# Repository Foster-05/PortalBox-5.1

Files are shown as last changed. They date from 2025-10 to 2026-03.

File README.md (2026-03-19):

# Portal Box 5.1.1
## A project by Bucknellians for Bucknellians, since 2013
   

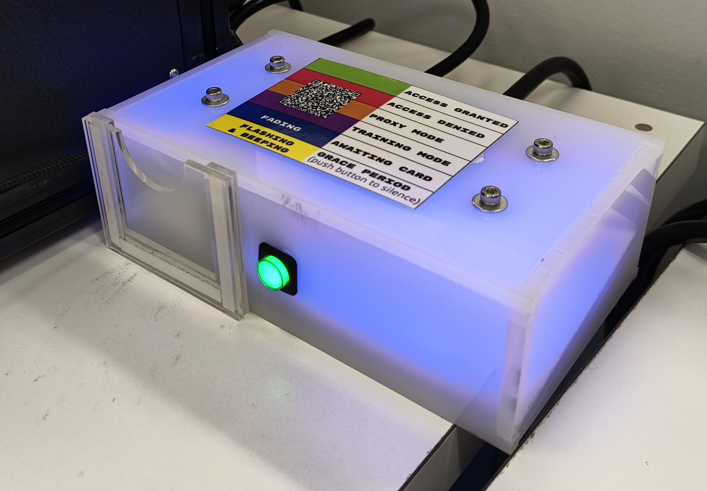
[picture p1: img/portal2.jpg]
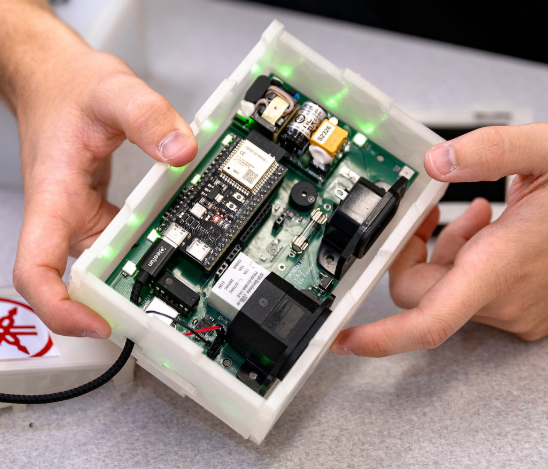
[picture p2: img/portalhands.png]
v5.0.6 while in progress
 

*The currently implemented Portalbox, v2, in the Maker-E connected to a Prusa XL (left) and a v5.0.6 prototype (right).*

## Background
The Portalbox is an open-source makerspace management project. It originated at Bucknell University, in our makerspace the "Maker-E", and intends to spread worldwide, allowing makerspaces to control their equipment and their users as they see fit. The Portalbox focuses on using interlocks to control power to equipment, such as 3D printers or laser cutters, based on the RFID cards that each student possesses. I had the opportunity to work on v5 of the Portalbox over the summer of 2025, continuing into the academic year 25-26.

The Portalbox has been an ongoing project for roughly a decade, remaining open-source and created by students throughout its lifetime. Professor Joe Hass and software engineer TKEgan on GitHub have historically maintained the project for both firmware and backend development, including but not limited to the database and website access that's used by student techs to change permissions to each Portalbox. Find more information about the backend at [their Github](https://github.com/Bucknell-ECE/PortalBox-ManagementPortal).

<details>

<summary> Previous Implementation </summary>

## Current Implementation

Current Portalbox implementation in the Maker-E

As it stands, the Portalbox is in the MakerE and for the most part, working as intended. It includes a very simple I/O: A slot for an RFID card, a simple pushbutton, and on the back two power ports and a reset button. It utilizes a finite state machine design to work with RFID reader and button input to ascern what mode of functionality it should be in. As much of this functionality has been retained for the next iteration. 

Use of the current Portalbox is very simple, intentionally so. Simply place your RFID card, programmed by a technician or makerspace administrator, into the card slot. The Portalbox will light blue if you are marked as certified in an SQL database, and red if you're not. If it determines that you are certified, it will activate the power interlock and allow wall power to flow to the machine that it's connected to, be it a 3D printer, laser cutter, or soldering iron. When you remove your card, the box will begin blinking yellow and beeping at you. Pressing the button on the front will exit this "grace mode". Putting your card back in will accomplish the same as putting your card in originally. However, if you place in a card programmed as a "proxy card", the box will light orange and remain on. The result is that you may use the machine or leave it running, but keep your assigned RFID card with you. Finally, if a user assigned as a trainer in the database takes their card out of the box, a non-certified user may place theirs as a replacement. The box will light purple for "training" mode, allowing the user to temporarily keep the equipment active while learning how to use it. After they have been trained on the piece of equipment a technician can certify them so they may use it in the future.

Moving into developing a Version 5, we maintained several goals in mind: shrinking the footprint, increasing speed and reliability, and maintaining or improving functionality. The physical box is significantly smaller than its predecessor, reducing by an overall 11 square centimeters. Our improved platform has yet to be tested firmware-wise, but we hope the new microcontroller will significantly improve response times and state detection accuracy. Our modular approach to design and implementation has allowed for increased functionality and the previous design with a slot and button is still available if users so wish.
</details>

<details open>
<summary>Technical information</summary>

## Technical
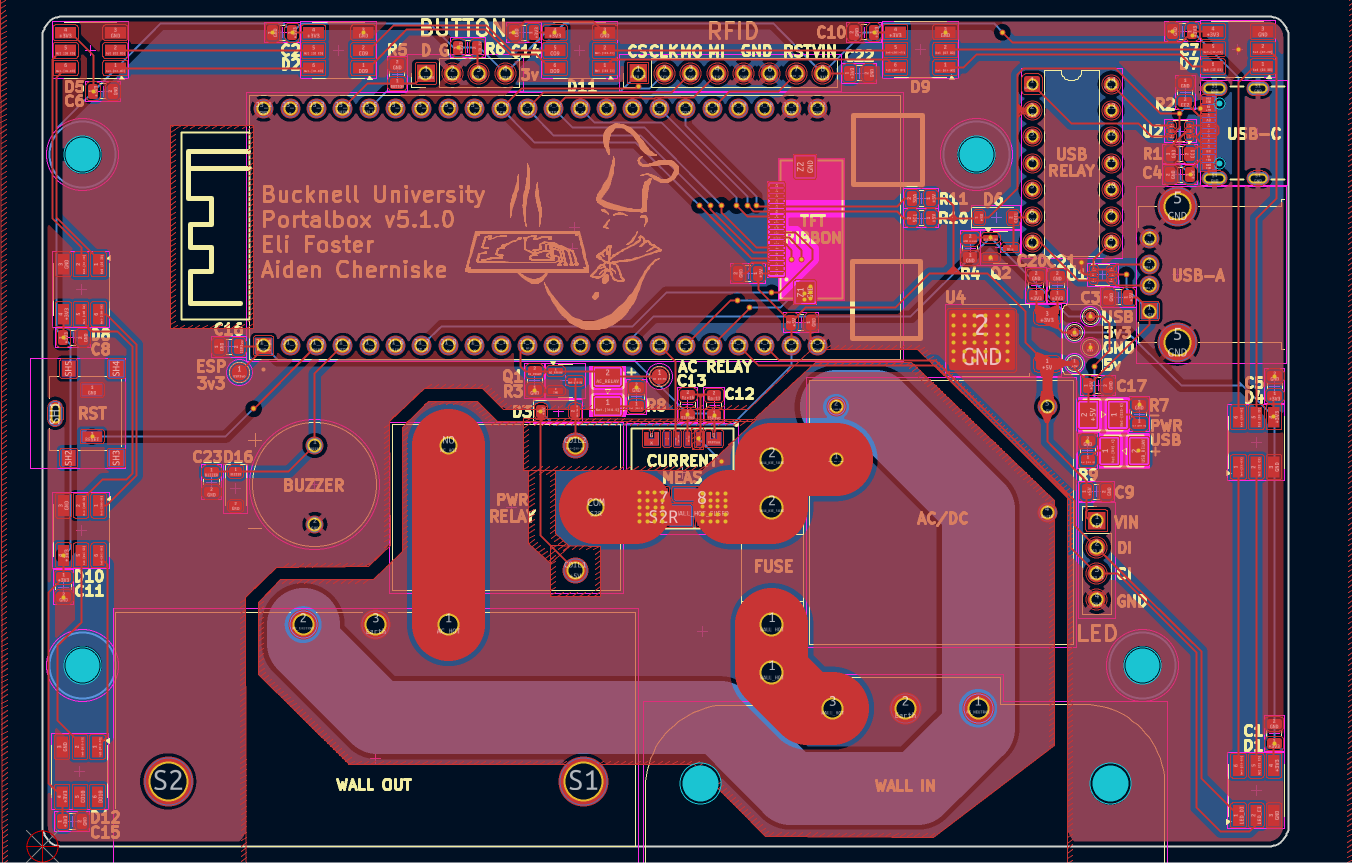
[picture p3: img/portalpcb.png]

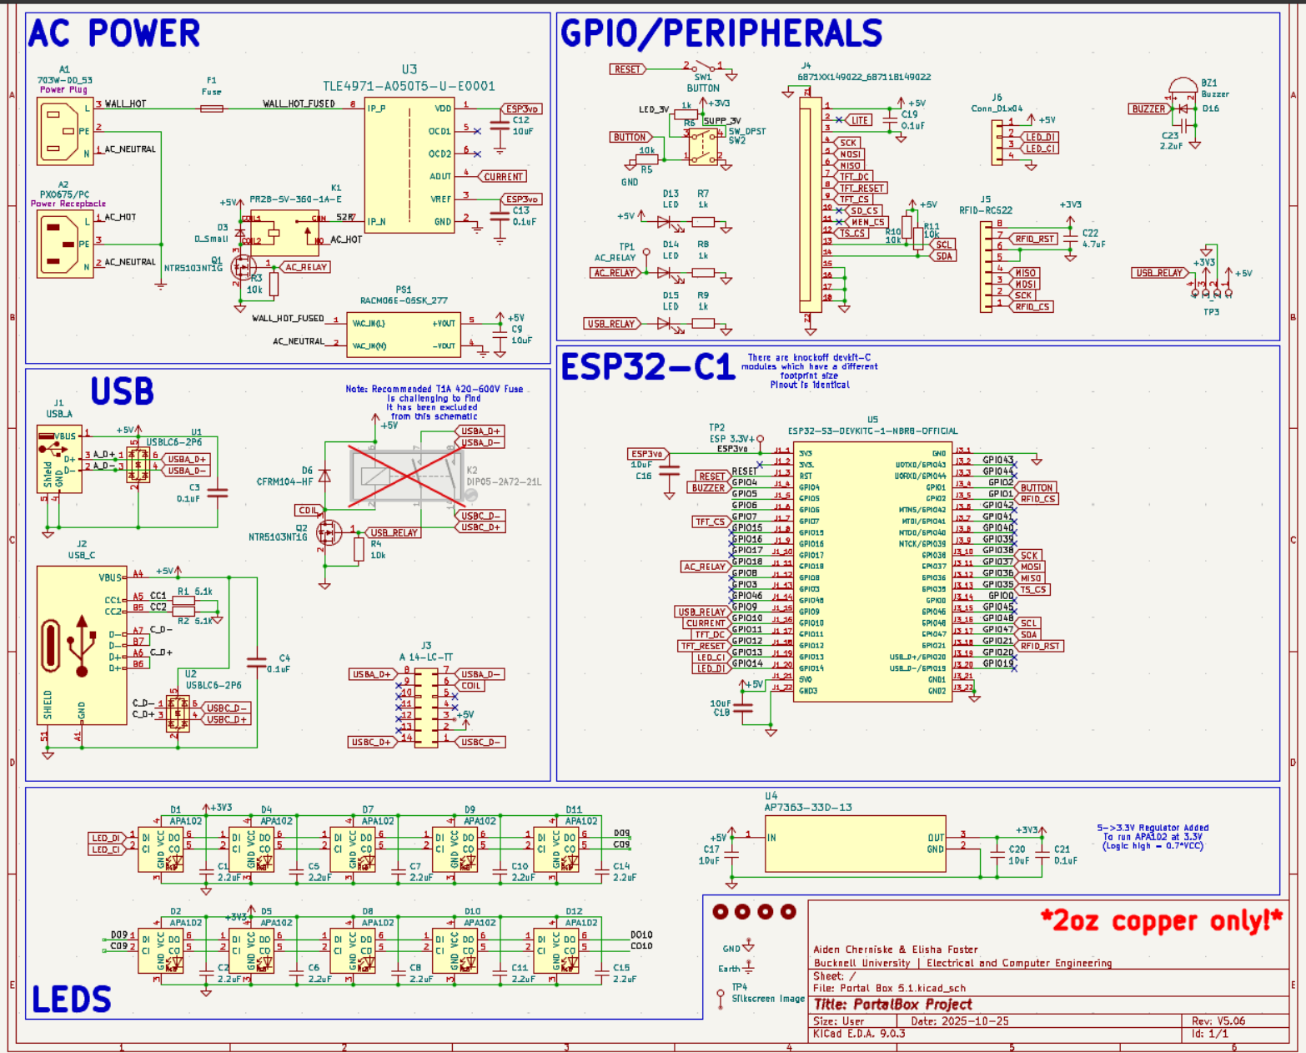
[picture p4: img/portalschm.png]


*Portalbox v5.1.0 layout (left) and schematic (right)*

<details>
<summary>Power Interlock</summary>

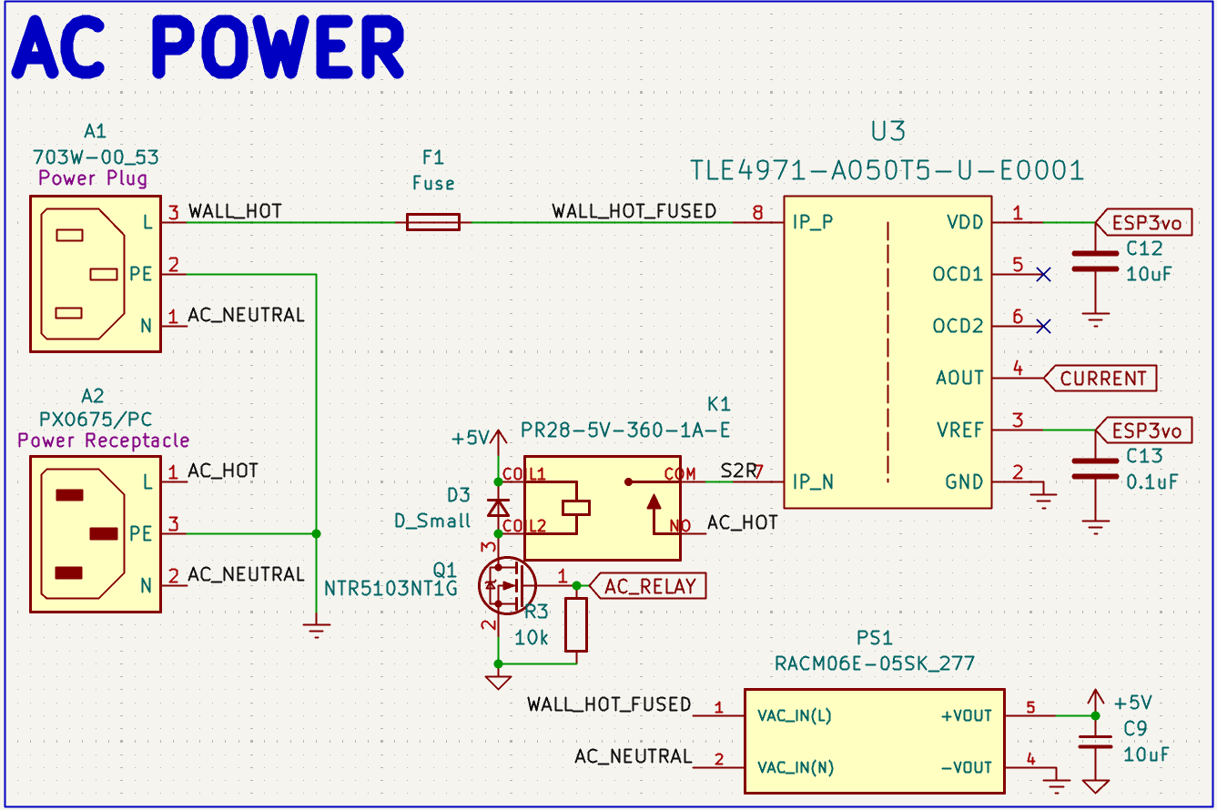
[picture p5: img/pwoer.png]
Schematic view of AC Power section for v5.1.0

### Overview
The Portalbox itself is powered off of 120Vrms from the wall, allowing for simpler placement and no worries or frustrations regarding battery power, lifetime, and so on. We use a hefty AC/DC converted to provide 5v power to the rest of the Portalbox, including the ESP32. We use relays to interlock wall power in between our two ports, one IEC C13 and one IEC C14. The female C13 is intended to be connected to wall power, while the male C14 is 15A fused output to makerspace equipment. We also include a current measurement IC to monitor power draw from a machine and monitor relay accuracy. Ensure that only 2 ounce copper is used when manufacturing: trace widths have been calculated to 2oz and traces may turn into fuses if incorrectly manufactured.
### Relay
We chose a [CUI Devices 20A relay](https://www.digikey.com/en/products/detail/same-sky-formerly-cui-devices/PR28-5V-360-1A-E/22522201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 "Digikey") to ensure that our fuse would disconnect the circuit before any parts become damaged. The relay accepts the hot line from the wall and outputs it to the current measurement IC when the relay is activated. Activation is done using a simple [NMOS transistor](https://www.digikey.com/en/products/detail/diodes-incorporated/2N7002K-7/1934378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 "Digikey") circuit to allow for a 3v GPIO pin from the ESP32 to activate the relay using 5v (its required activation voltage). This specific transistor was chosen for availability, being pre-stocked in our space.

### Current Measurement
We're measuring current flowing from the wall out to the C14 port for a multitude of reasons. With proper implementation, this would allow for a measurement of "normal" current draw for any given machine, thus allowing continuous monitoring and flagging of any unusual or concerning behavior remotely. It would also allow us to retrieve records or throw a flag if our maximum of 15A is reached, thus requiring us to replace the onboard fuse. This would require some implementation with the existing MariaDB SQL database to store said current data and/or flags. Measurement is accomplished using an [Infineon IC](https://www.digikey.com/en/products/detail/infineon-technologies/TLE4971A050T5UE0001XUMA1/18700354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 "Digikey") for this specific purpose. It's capable of +-120A, being much more than we need. It ouputs a variable voltage that depends on the current flowing through two major pads, allowing for later conversion into what specific current is being measured.
</details>

<details>
<summary>USB Interlock</summary>

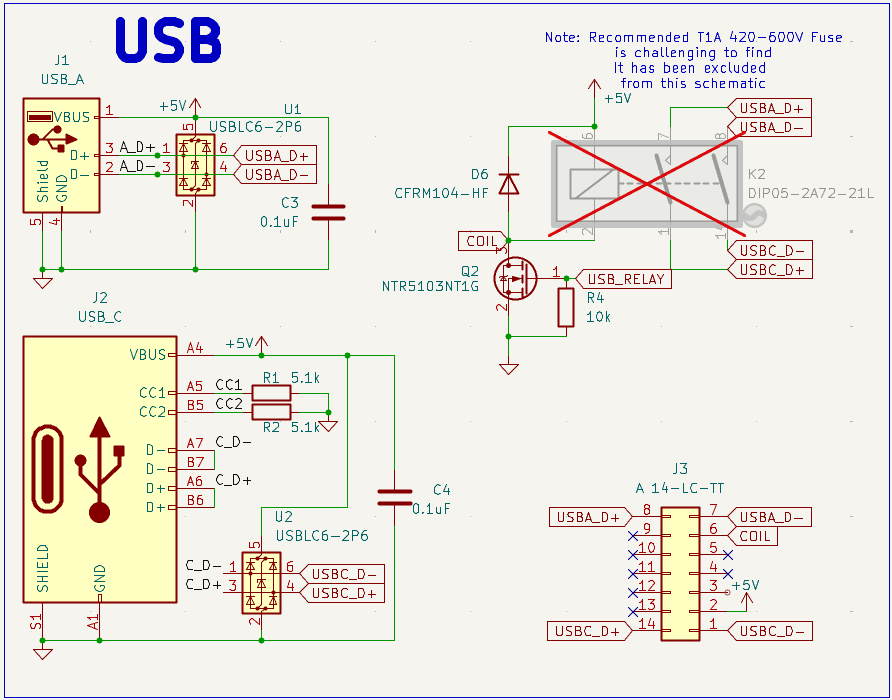
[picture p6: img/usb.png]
Schematic view of USB interlock section for v5.1.0

### Overview
The Portalbox is equipped to provide data interlock through USB 2.0 between a USB-A port and a USB-C port. This is for specific applications such as the Maker-E's laser cutter, where proprietary power supply makes power interlock difficult. However, one is able to connect USB cables in between the cutter and a dedicated device to restrict data transfer of files required for laser cutting. It uses a similar relay structure to the power interlock to allow for robust switching.

### Relay
We use a [Standex-Meder](https://www.digikey.com/en/products/detail/standex-meder-electronics/DIP05-2A72-21L/2765346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 "Digikey") DIP relay to allow for switching of data lines. It allows for simultaneous switching of two signals, which was necessary to interlock the D+/D- lines found in the USB 2.0 protocol. This particular relay may be out of stock and a Littelfuse equivealent is available. It's shown as excluded from the board in the schematic because we use a different [DIP header](https://www.digikey.com/en/products/detail/assmann-wsw-components/A-14-LC-TT/821743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 "Digikey") J3 to allow for active switching of relays. Modularity is a big focus of the Portalbox, so switching of any components is ideal when possible.

### USB port design
We use typical four-pin USB-A 2.0 ports as well as USB-C ports capable of 3.0 on the board files seen above. They follow best practices found in the datasheet for design, including but not limited to ESD protection with diode system ICs U1 and U2. Both ports are always powered with 5v and have no data connection unless the above relays are active.
</details>

<details>
<summary>Peripherals and GPIO</summary>

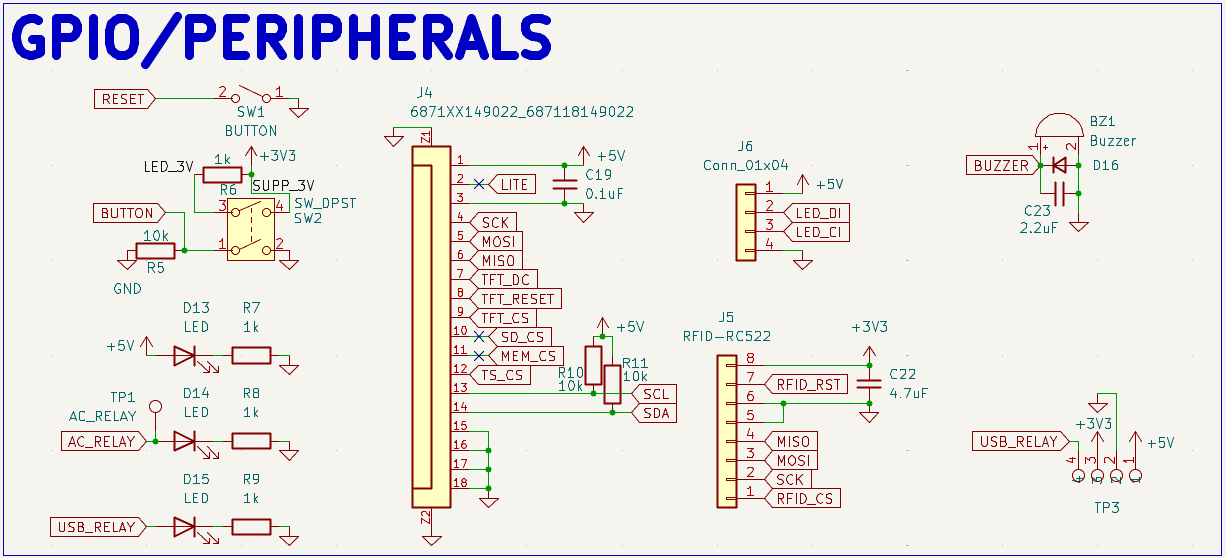
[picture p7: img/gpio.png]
Schematic view of GPIO section for v5.1.0


While the power and data interlocks are the meat and potatoes of the Portalbox, our peripherals and GPIO is the seasoning. These focus on all of our miscellaneous functions, both new and old. Historically the boxes have been as simple to use as possible, including simply a card slot, single pushbutton, and RGB LEDs for feedback. This functionality has been retained, but we hope to significantly improve it for future use.

### Casing
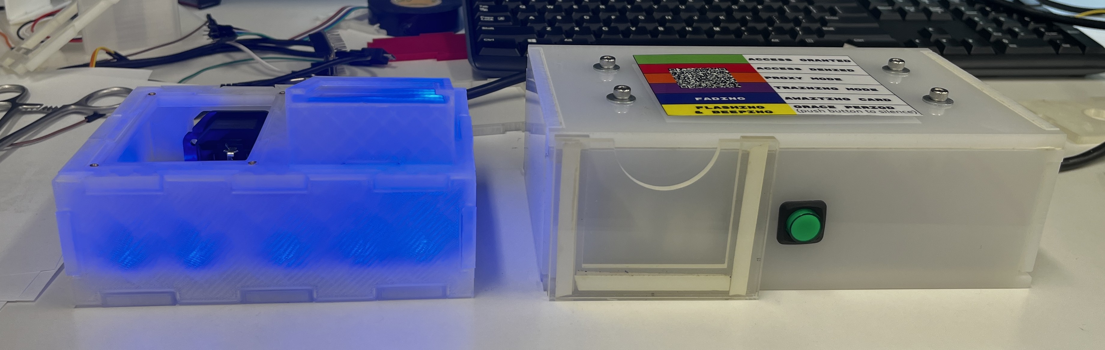
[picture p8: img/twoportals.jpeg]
Side-by-side old and new versions of the Portalbox.

Size has been another important factor of consideration while moving through the current version of the Portalbox. Initial versions were vertically stacked components, so they were relatively compact and fit in the space well. The versions currently implemented moved away from the vertical architecture, so they expanded significantly in footprint next to machinery in the Maker-E. Beginning our project, we wanted to ensure that we could shrink this footprint at least a little bit so the Portalbox would be more usable and widely applicable for most makerspaces. Above is pictured a version 5.0.6 (left), which is the same size as a version 5.1, next to a currently implemented Portalbox (right). The difference is apparent.

#### Materials and Design

Previously Portalboxes were all made out of lasercut acrylic, which was intentionally a semi-transparent material designed to be opaque but let LED light through to color the box itself. This design has worked very well, but we had serveral quarrels with it when starting the project. First and foremost, it was very painful to construct. The pieces had to fit together very precisely and use Very Heavy Bond tape to stick together long-term. The acrylic material was also expensive to acquire. We found that the original reasoning to choose acrylic was that makerspaces would be able to manufacture their own cases if they had a laser cutter on hand, as we did. Considering this design decision, we chose to move the Portalbox to a 3D printed enclosure. Nowadays, especially in the ECE space, 3D printers are a staple of iterative design and most makerspaces have access to at least one. We tested multiple filament types and determined that Jessie Transparent PLA was strong yet still let through the appropriate amount of light from LEDs mounted on the board. Gyroid infill patterns also provide fun effects! While designing the case, we were focused on ensuring modularity and ease of use. The case is designed to snap together using dovetails and require no adhesive or tape to stay together long-term. Said dovetails also provide interesting opportunities for modularity.

#### Modularity

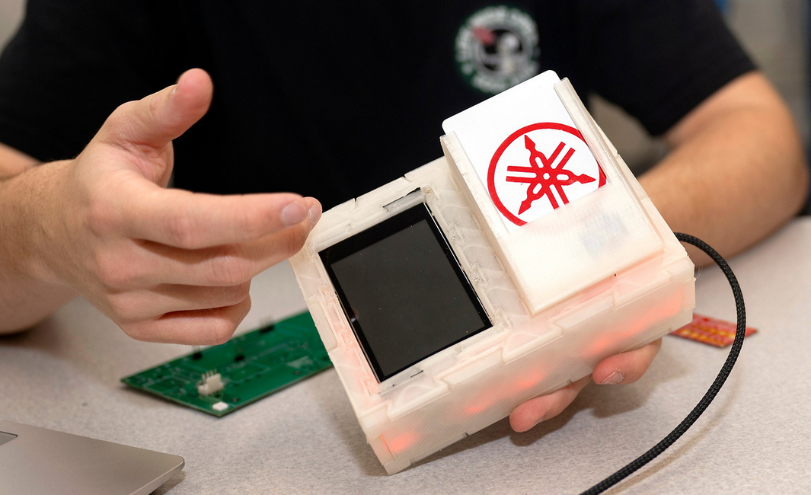
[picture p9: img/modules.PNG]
Top side of the Portalbox showcasing a card reader and touchscreen module installed.

Utilizing the 3D printed nature of the case and the dovetail design, we determined a method to standardize our design and allow for some of the open-source mindset to enhance the Portalbox. First and foremost, the Portalbox case was designed with options in mind. There are multiple inputs and outputs that one can choose to use with the Portalbox and that will work natively and immediately with the firmware, all of which have case pieces designed to fit them. There are also options to fit the same inputs and outputs on different sides of the case for alternate mounting options. The peak of modularity can be seen on the top part of the case, where it simply features two large holes containing dovetails to slot other pieces into. With this design, we're able to manufacture modules which best fit our use-case: from touchscreens to buttons to card readers, it provides nearly unlimited opportunity to design what you want for your makerspace and customize your Portalbox appropriately. We hope that the nature of this design will encourage others to participate and begin designing alternate components that will work with all the previous ones we've provided as a starting point.

### User Feedback

Along with the above mention of modularity, we wanted to ensure that this version of the Portalbox would be able to continue in its current function as well as extend to new applications. Therefore, we kept all of the same standard inputs and outputs: a piezo buzzer to alert users, RGB addressable LEDs to provide status of the box, a simple button for a multifunctional input, and an RFID reader for the typical "slot" application. We also extended some of the more technical user feedback by including test points for important nets, as well as mono-color feedback LEDs for 5v power, AC relay activation, and USB relay activation. A reset button broken out to the user is also available in the case of a manual reset becoming necessary. However, with the aforementioned modular case, we also included some other options for administrators. The firmware provides for a "tap" mode, where users no longer have to leave their card inside a Portalbox to use equipment. They can simply tap it on the case, and a "proxy" mode will be handled all in software instead of requiring physical proxy cards. We also added a ribbon cable connector for Adafruit's Eye-SPI technology, making interfacing with one of their [ILI9341 capacitative touch displays](https://www.adafruit.com/product/2090 "Adafruit") simple to implement. We hope that this will spruce up our space and make the Portalboxes even easier to use, while not precluding previous use-cases.
</details>

<details>
<summary>Microcontroller</summary>

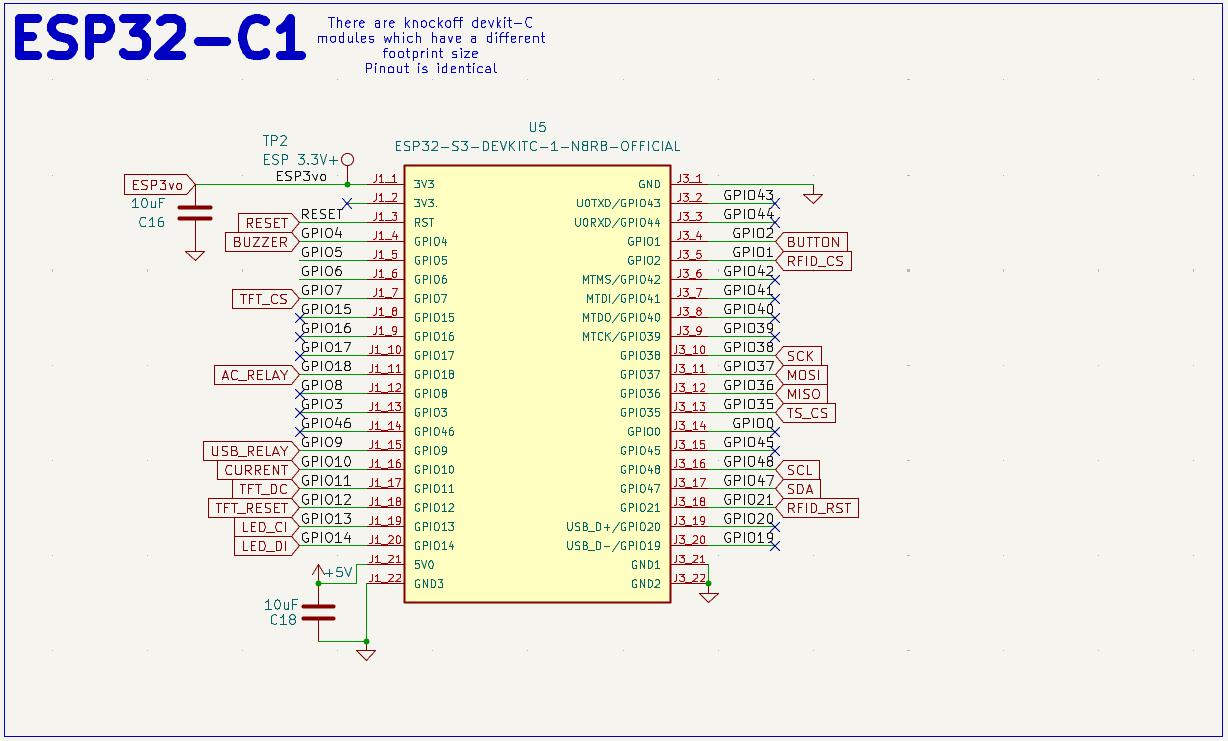
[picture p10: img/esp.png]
Schematic view of MCU section for v5.1.0

### History
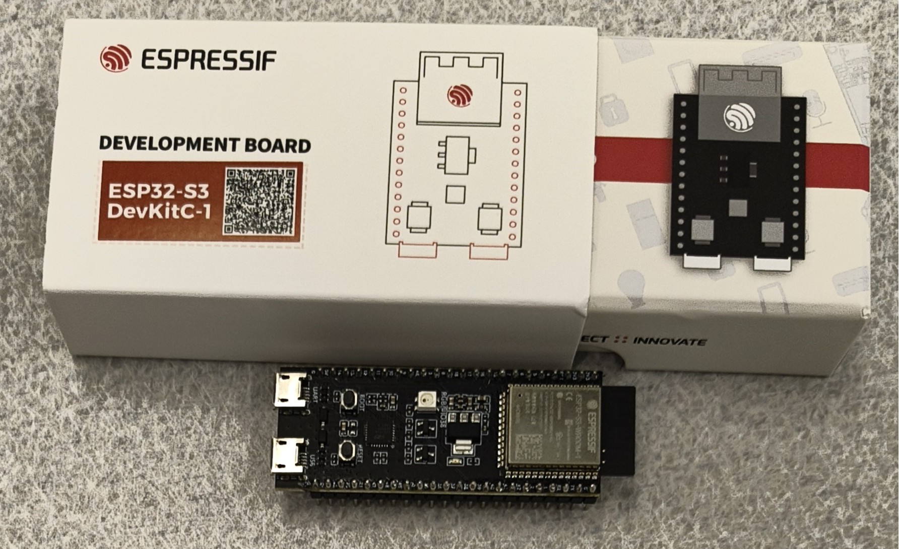
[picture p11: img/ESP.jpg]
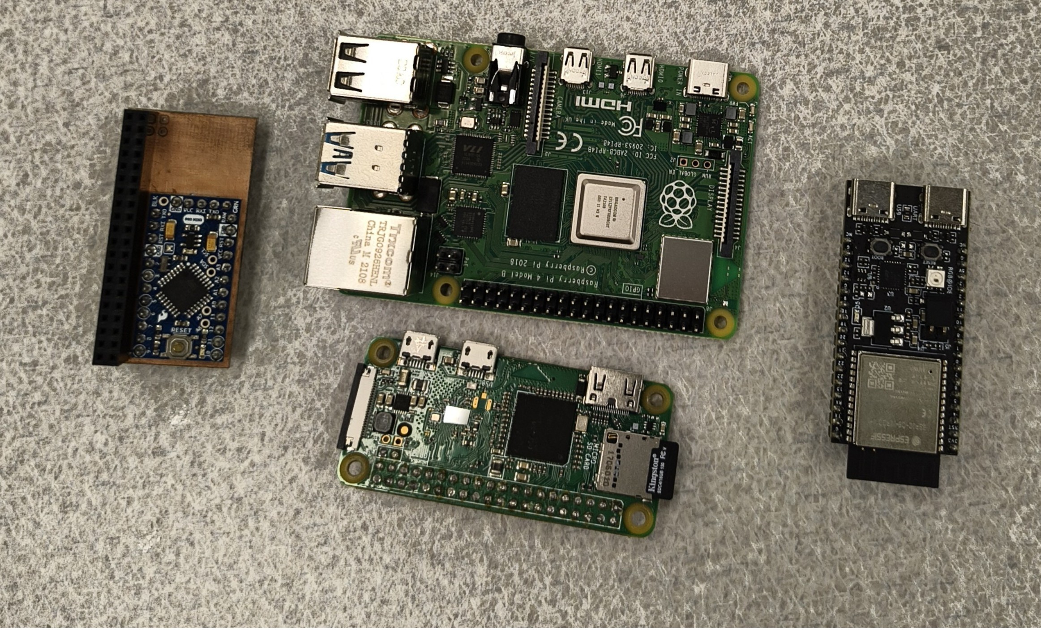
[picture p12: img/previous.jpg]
 

Historically, the Portalbox has been through every microcontroller you can think of. An original iteration used RP2040 breakout boards to do all processing on the platform, and connected a Pi Zero W to it for WiFi and API calling capabilities. Some time after that, a Raspberry Pi 4 was used to accomplish both tasks on one platform - at this point the Portalbox was running a full Linux OS with some firmware stored on it that would run upon boot.

During our time with the project, one of our main goals was to move platform to something that was smaller, less expensive, and more apt for the task. We chose to use the ESP32 platform, as it would still give us full internet capabilities while in a smaller form factor and with plenty of processing power to do the job. This turned our major limitation into GPIO.

We deliberately chose to utilize a [full devkit from Espressif](https://www.digikey.com/en/products/detail/espressif-systems/ESP32-S3-DEVKITC-1-N8R8/15295894 "Digikey") instead of simply placing the chip on our board. This decision was made for a multitude of reasons, but chief among them was that it made our lives easier and will continue to be effective far into the future. Long story short, all of the onboard electronics already included allowed us to focus on development of our other systems instead of worrying about setting up JTAG and the like. It also allows us to simply replace an entire module if something fails in the future, meaning these boards will be able to be used far into the future by simply replacing components and preventing the trashing of an entire board due to an oversight or failure.

Accordingly, we chose the Espressif devkit because they provide the most complete hardware output, as well as a fleshed out ESP-IDF toolchain for natively flashing boards if necessary. Specifically, the Espressif ESP32-S3-Devkit-C1 breaks out nearly all of the onboard GPIO so we can fit in all of our components that we need to and leave several pins for further expansion if we so desire. We originally began development with the ESP32-C6 devkit, but found it was too limited for our needs. The S3, specifically the C1-N8R8 revision, takes a larger footprint of the board but has proportionately more GPIO. Also beware of off-brand or alternate suppliers of devkits, as we found some with the same functionality but a very different physical footprint, being longer and skinnier. Be aware of the difference and make sure to purchase from Digikey or Adafruit. 

At different points we utilized ESP-IDF to flash our devkits with a custom build of Micropython. All firmware for the Portalbox is currently written in Micropython. There's a big focus on connectivity, and getting access to WPA3-Enterprise networks was a goal of ours. These networks are extremely common at universities and would make spreading the Portalbox much easier if they will natively hook up to existing WiFi networks. This is currently not implemented, as Micropython does not natively support Enterprise networks. There's a pending pull request that would implement it, so hopefully soon this capability will be added. In the meantime, our boxes are connected to the hidden Personal-class network on campus used in our engineering building.
</details>

<details>
<summary>Certification Compliance</summary>
The Portalbox has been designed to as closely as possible comply with IPC-2221 for General Design, and more specifically for IPC-2222 Rigid design specifications. Please make us aware of any discrepancies that may come up.
</details>

</details>

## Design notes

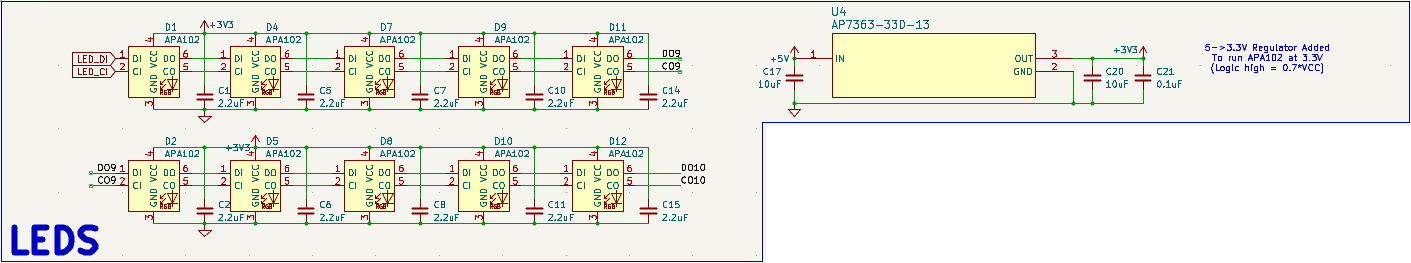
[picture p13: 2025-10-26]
img/leds.png

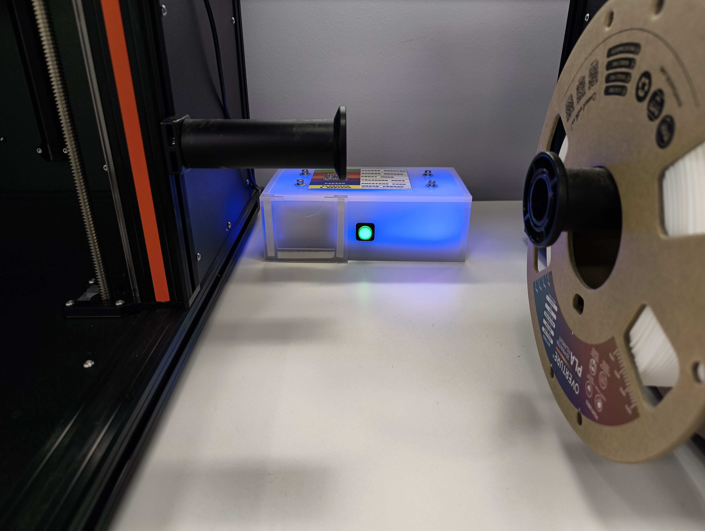
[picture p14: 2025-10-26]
img/portal1.jpg

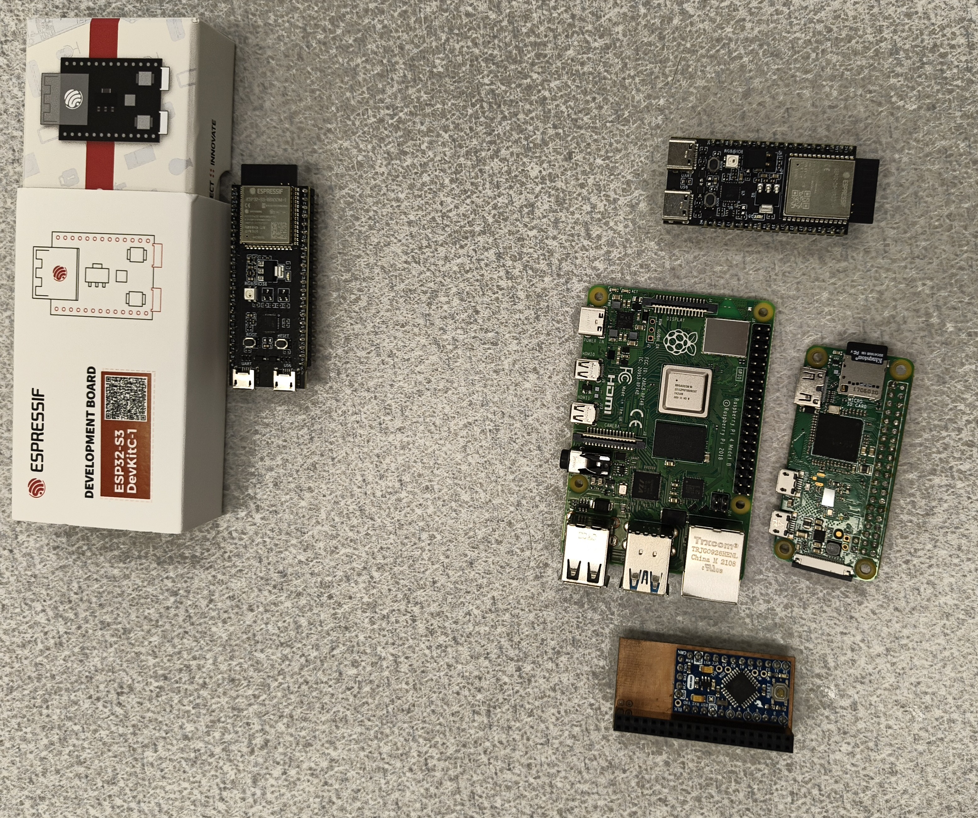
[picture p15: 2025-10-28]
img/MCUs.jpg

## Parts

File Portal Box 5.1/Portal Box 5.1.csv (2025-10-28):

Reference | Value | Qty | MakerStock? | Need for 10/25/25 run? | Link
A1 | QUALTEK_703W-00_53 | 1 | N | N | https://www.digikey.com/en/products/detail/qualtek/703W-00-53/245560
A2 | PX0675/PC | 1 | N | N | https://www.digikey.com/en/products/detail/bulgin/PX0675-PC/1980709
BZ1 | Buzzer, XDCR_AI-1223-TWT-3V-2-R | 1 | N | Get back from Stewart >:( | https://www.digikey.com/en/products/detail/pui-audio-inc/ai-1223-twt-5v-7/21689820
C1,C2,C5,C6,C7,C8,C10,C11,C14,C15,C23 | 2.2uF | 11 | Y | N
C3,C4,C13,C19,C21 | 0.1uF | 5 | Y | N
C9,C12,C16,C17,C18,C20 | 10uF | 6 | Y | N
C22 | 4.7uF | 1 | Y | N
D1,D2,D4,D5,D7,D8,D9,D10,D11,D12 | APA102 | 10 | N | N
D3,D16, D6 | CFRM104-HF | 3 | Y | N
D13,D14,D15 | LED, 732-13433-1-ND | 3 | Y | N
F1 | Fuse | 1 | N | N
J1 | USB_A, AMPHENOL_87520-0010ALF | 1 | N | Y | https://www.digikey.com/en/products/detail/amphenol-cs-fci/87520-0010ALF/1552363
J2 | USB_C, GCT_USB4105-GF-A | 1 | N | N | https://www.digikey.com/en/products/detail/gct/USB4105-GF-A/11198441
J3 | A 14-LC-TT | 1 | N | N
J4 | Ribbon cable connector, 732-6001-1-ND | 1 | N | Y | https://www.digikey.com/en/products/detail/w%C3%BCrth-elektronik/687118149022/5047793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
J5 | RFID-RC522 | 1 | N | N
K1 | PR28-5V-360-1A-E | 1 | N | N
K2 | DIP05-2A72-21L | 1 | N | N
PS1 | RACM06E-05SK_277 | 1 | N | Y | https://www.digikey.com/en/products/detail/recom-power/RACM06E-05SK-277/21334017
Q1,Q2 | NTR5103NT1G | 2 | Y | N
R1,R2 | 5.1k | 2 | Y | N
R3,R4,R5,R10,R11 | 10k | 5 | Y | N
R6,R7,R8,R9 | 1k | 4 | Y | N
SW1 | RESET BUTTON, SW_TL3336AF160Q | 1 | N | N | https://www.digikey.com/en/products/detail/e-switch/TL3336AF160Q/14123602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
SW2 | SW_DPST (BUTTON), adafruit 1440 | 1 | Y | Y? Closet? Not sure | https://stock.maker.bucknell.edu/product/16mm-illuminated-pushbutton/
U1,U2 | USBLC6-2P6 | 2 | N | Y | https://www.digikey.com/en/products/detail/stmicroelectronics/USBLC6-2P6/1007440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
U3 | TLE4971-A050T5-U-E0001 | 1 | N | Y | https://www.digikey.com/en/products/detail/infineon-technologies/TLE4971A050T5UE0001XUMA1/18700354
U4 | AP7363-33D-13 | 1 | Y | N
U5 | ESP32-S3-DEVKITC-1-N8R8-OFFICIAL | 1 | N | N

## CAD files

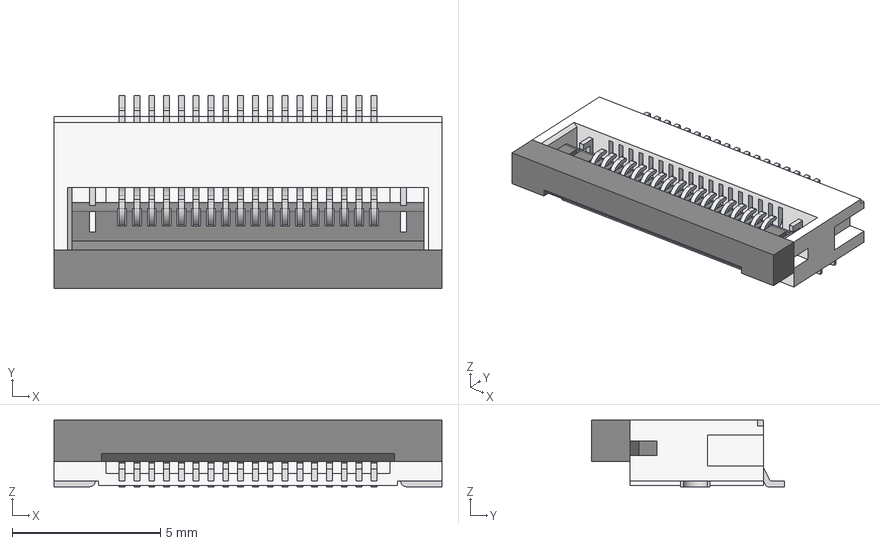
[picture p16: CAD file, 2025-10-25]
Portal Box 5.1/Components/6871XX149022_687118149022.step
13.1 x 6.50 x 2.25 mm
6871xx149022_Pin x 18
6871xx149022_Patte
6871xx149022_Patte2
687118149022_Actuator

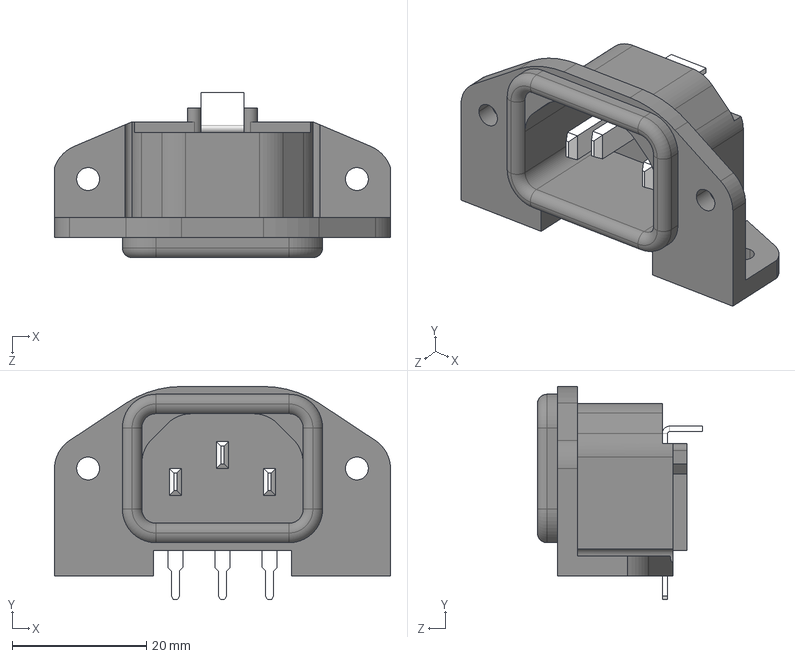
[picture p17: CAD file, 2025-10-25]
Portal Box 5.1/Components/703W_00_53/703W-00_53.step
50.0 x 31.7 x 24.6 mm

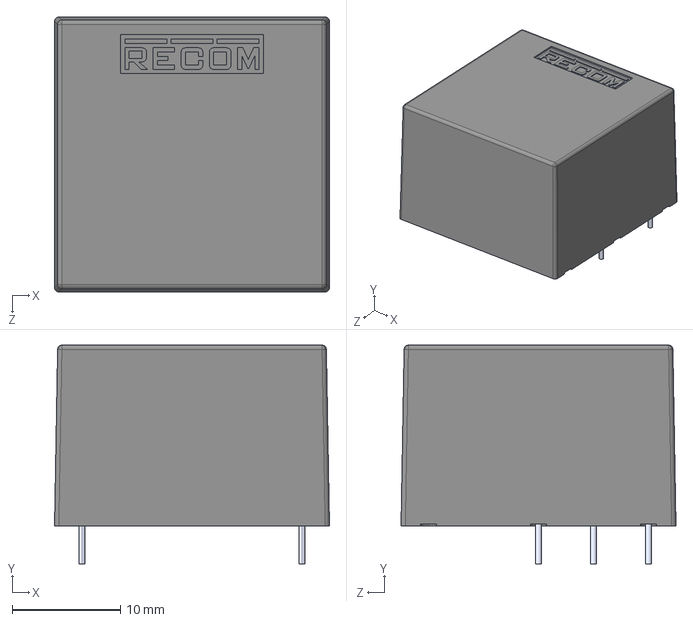
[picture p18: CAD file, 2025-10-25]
Portal Box 5.1/Components/RACM06E-05SK_277.step
25.4 x 20.2 x 25.4 mm

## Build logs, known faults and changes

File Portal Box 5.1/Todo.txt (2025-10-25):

-ask matt about current sensor ground pad solid vs thermal relief, one pad relief and ths solid X
	-solid shouldn't matter, run a trace out if necessary or via in pad
-fillet edges X
-change pin assignments for buzzer (usb) and current sensor (adc) X
-cross reference board uart/rtc/usb X
	-I feel good about spi assignments for FastSPI, make sure CS can be anywhere
-investigate rfid reset issue X
- stitching vias
	-plugin?
- fix ribbon cable routing, return currents on spi X
-Finish assigning pin X 

-silkscreening

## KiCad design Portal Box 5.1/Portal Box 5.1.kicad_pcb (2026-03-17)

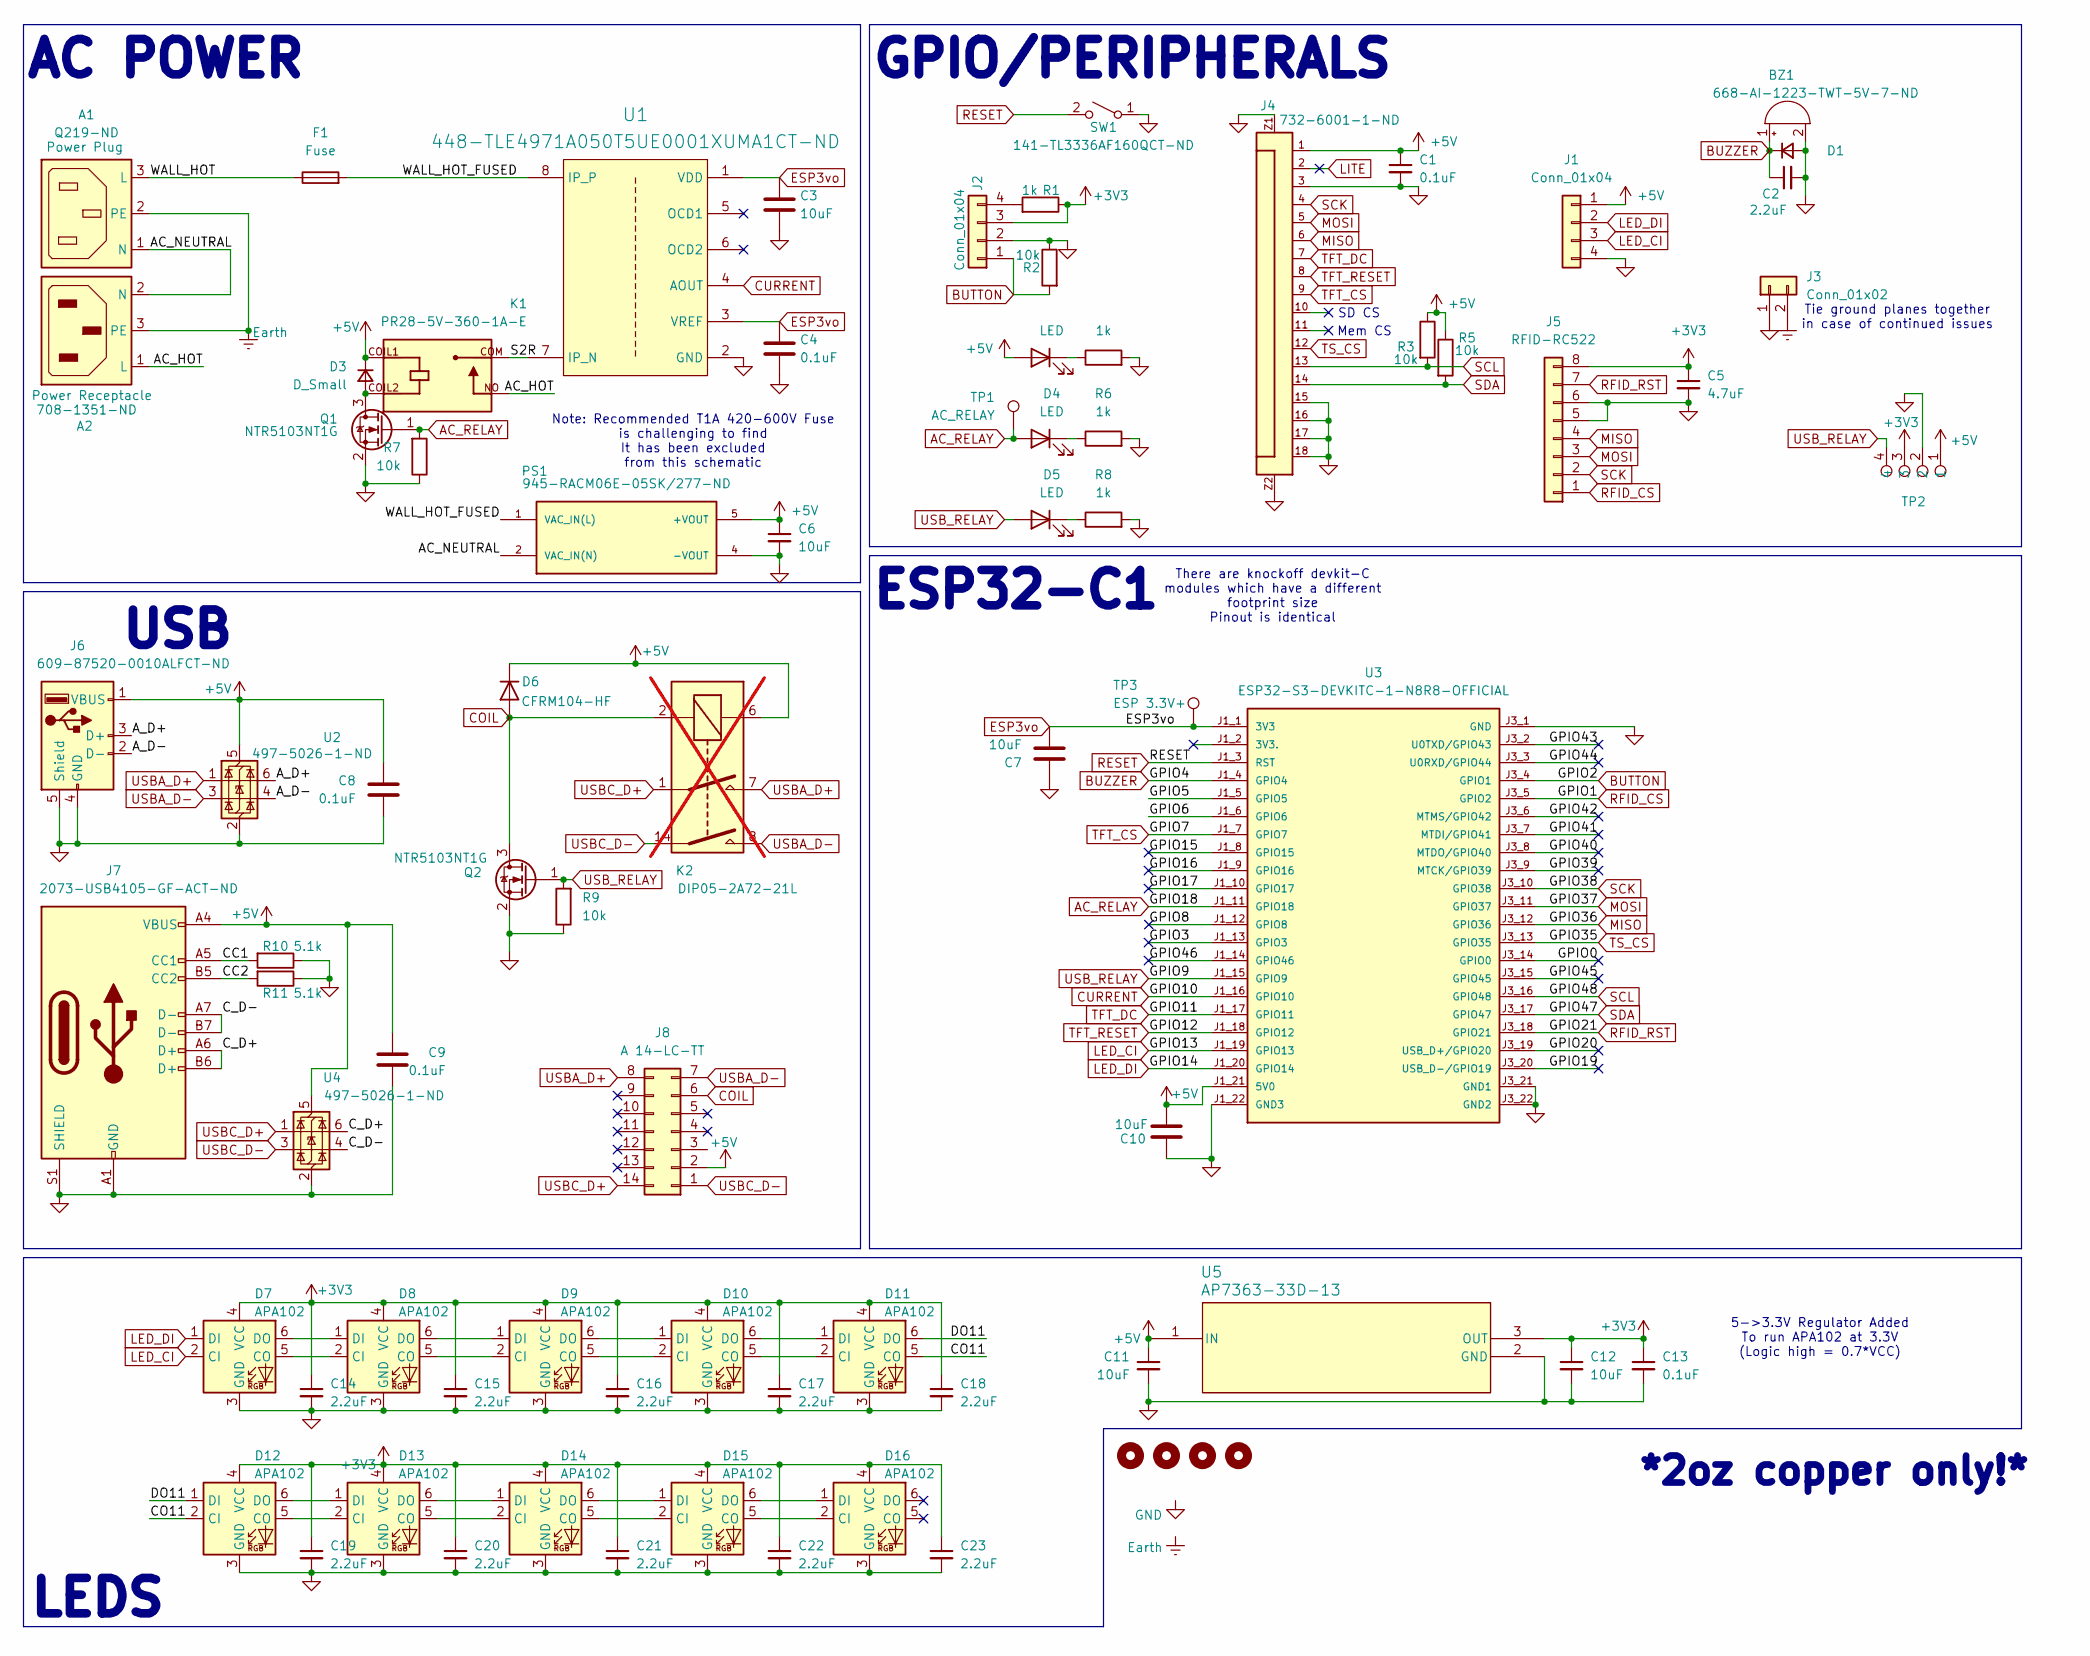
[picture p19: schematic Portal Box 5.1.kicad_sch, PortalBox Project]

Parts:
A1: Q219-ND; QUALTEK_703W-00_53; Part No Q219-ND
A2: 708-1351-ND; BULGIN_PX0675_PC
BZ1: 668-AI-1223-TWT-5V-7-ND; XDCR_AI-1223-TWT-3V-2-R
C1, C4, C8, C9, C13: 0.1uF; C_0805_2012Metric
C2, C14, C15, C16, C17, C18, C19, C20, C21, C22, C23: 2.2uF; C_0805_2012Metric
C3, C6, C7, C10, C11, C12: 10uF; C_0805_2012Metric
C5: 4.7uF; C_0805_2012Metric
D1, D3: D_Small; D_SOD-123
D2, D4, D5: LED; WL-SMTW_3528
D6: CFRM104-HF; D_SOD-123
D7, D8, D9, D10, D11, D12, D13, D14, D15, D16: APA102; LED_RGB_5050-6
F1: Fuse; Fuse_Custom
H1, H2, H3, H4: MountingHole; MountingHole_3.2mm_M3
J1, J2: Conn_01x04; PinHeader_1x04_P2.54mm_Vertical
J3: Conn_01x02; PinHeader_1x02_P2.54mm_Vertical
J4: 732-6001-1-ND; adafruit_ribbon_conn
J5: RFID-RC522; PinHeader_1x08_P2.54mm_Vertical
J6: 609-87520-0010ALFCT-ND; AMPHENOL_87520-0010ALF
J7: 2073-USB4105-GF-ACT-ND; GCT_USB4105-GF-A
J8: A 14-LC-TT; DIP-14_W7.62mm
K1: PR28-5V-360-1A-E; RELAY_PR28-5V-360-1A-E; PARTREV 1.01
K2: DIP05-2A72-21L; Relay_StandexMeder_DIP_LowProfile; not fitted
PS1: 945-RACM06E-05SK/277-ND; CONV_RACM06E-05SK_277; PARTREV PRELIMINARY
Q1, Q2: NTR5103NT1G; SOT-23
R1, R4, R6, R8: 1k; R_0805_2012Metric
R2, R3, R5, R7, R9: 10k; R_0805_2012Metric
R10, R11: 5.1k; R_0805_2012Metric
SW1: 141-TL3336AF160QCT-ND; SW_TL3336AF160Q
TP1: AC_RELAY; TestPoint_Pad_D1.5mm
TP2: FourTPs
TP3: ESP 3.3V+; TestPoint_Pad_D1.5mm
U1: 448-TLE4971A050T5UE0001XUMA1CT-ND; TLE4971
U2, U4: 497-5026-1-ND; SOT-666
U3: ESP32-S3-DEVKITC-1-N8R8-OFFICIAL
U5: AP7363-33D-13; TO-252-2

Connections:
+3V3: C5.1, C12.1, C13.1, C14.1, C15.1, C16.1, C17.1, C18.1, C19.1, C20.1, C21.1, C22.1, C23.1, D7.4 (VCC), D8.4 (VCC), D9.4 (VCC), D10.4 (VCC), D11.4 (VCC), D12.4 (VCC), D13.4 (VCC), D14.4 (VCC), D15.4 (VCC), D16.4 (VCC), J2.3, J5.8, R1.1, TP2.3, U5.3 (OUT)
+5V: C1.1, C6.1, C8.1, C9.1, C10.2, C11.1, D2.2 (A), D3.1 (K), D6.1 (K), J1.1, J4.1, J6.1 (VBUS), J7.A4 (VBUS), J7.A9 (VBUS), J7.B4 (VBUS), J7.B9 (VBUS), J8.2, K1.COIL1, K2.6, PS1.5 (+VOUT), R3.1, R5.1, TP2.1, U2.5 (VBUS), U3.J1_21 (5V0), U4.5 (VBUS), U5.1 (IN)
/AC_HOT: A2.1 (L), K1.NO
/AC_NEUTRAL: A1.1 (N), A2.2 (N), PS1.2 (VAC_IN(N))
/A_D+: J6.3 (D+), U2.6 (I/O1)
/A_D-: J6.2 (D-), U2.4 (I/O2)
/CC1: J7.A5 (CC1), R10.2
/CC2: J7.B5 (CC2), R11.2
/CO11: D11.5 (CO), D12.2 (CI)
/C_D+: J7.A6 (D+), J7.B6 (D+), U4.6 (I/O1)
/C_D-: J7.A7 (D-), J7.B7 (D-), U4.4 (I/O2)
/DO11: D11.6 (DO), D12.1 (DI)
/GPIO0: U3.J3_14 (GPIO0)
/GPIO3: U3.J1_13 (GPIO3)
/GPIO5: U3.J1_5 (GPIO5)
/GPIO6: U3.J1_6 (GPIO6)
/GPIO8: U3.J1_12 (GPIO8)
/GPIO15: U3.J1_8 (GPIO15)
/GPIO16: U3.J1_9 (GPIO16)
/GPIO17: U3.J1_10 (GPIO17)
/GPIO19: U3.J3_20 (USB_D-/GPIO19)
/GPIO20: U3.J3_19 (USB_D+/GPIO20)
/GPIO39: U3.J3_9 (MTCK/GPIO39)
/GPIO40: U3.J3_8 (MTDO/GPIO40)
/GPIO41: U3.J3_7 (MTDI/GPIO41)
/GPIO42: U3.J3_6 (MTMS/GPIO42)
/GPIO43: U3.J3_2 (U0TXD/GPIO43)
/GPIO44: U3.J3_3 (U0RXD/GPIO44)
/GPIO45: U3.J3_15 (GPIO45)
/GPIO46: U3.J1_14 (GPIO46)
/S2R: K1.COM, U1.7 (IP_N)
/WALL_HOT: A1.3 (L), F1.1
/WALL_HOT_FUSED: F1.2, PS1.1 (VAC_IN(L)), U1.8 (IP_P)
AC_RELAY: D4.2 (A), Q1.1 (G), R7.2, TP1.1, U3.J1_11 (GPIO18)
BUTTON: J2.1, R2.2, U3.J3_4 (GPIO1)
BUZZER: BZ1.1 (+), C2.1, D1.1 (K), U3.J1_4 (GPIO4)
COIL: D6.2 (A), J8.6, K2.2, Q2.3 (D)
CURRENT: U1.4 (AOUT), U3.J1_16 (GPIO10)
ESP3vo: C3.1, C4.1, C7.2, TP3.1, U1.1 (VDD), U1.3 (VREF), U3.J1_1 (3V3)
Earth: A1.2 (PE), A2.3 (PE), J3.2
GND: BZ1.2 (-), C1.2, C2.2, C3.2, C4.2, C5.2, C6.2, C7.1, C8.2, C9.2, C10.1, C11.2, C12.2, C13.2, C14.2, C15.2, C16.2, C17.2, C18.2, C19.2, C20.2, C21.2, C22.2, C23.2, D1.2 (A), D7.3 (GND), D8.3 (GND), D9.3 (GND), D10.3 (GND), D11.3 (GND), D12.3 (GND), D13.3 (GND), D14.3 (GND), D15.3 (GND), D16.3 (GND), J1.4, J2.2, J3.1, J4.3, J4.15, J4.16, J4.17, J4.18, J4.Z1, J4.Z2, J5.5, J5.6, J6.4 (GND), J6.5 (Shield), J7.A1 (GND), J7.A12 (GND), J7.B1 (GND), J7.B12 (GND), J7.S1 (SHIELD), PS1.4 (-VOUT), Q1.2 (S), Q2.2 (S), R2.1, R4.2, R6.2, R7.1, R8.2, R9.1, R10.1, R11.1, SW1.1 (A), TP2.2, U1.2 (GND), U2.2 (GND), U3.J1_22 (GND3), U3.J3_1 (GND), U3.J3_21 (GND1), U3.J3_22 (GND2), U4.2 (GND), U5.2 (GND)
LED_CI: D7.2 (CI), J1.3, U3.J1_19 (GPIO13)
LED_DI: D7.1 (DI), J1.2, U3.J1_20 (GPIO14)
LITE: J4.2
MISO: J4.6, J5.4, U3.J3_12 (GPIO36)
MOSI: J4.5, J5.3, U3.J3_11 (GPIO37)
unnamed: D2.1 (K), R4.1
unnamed: D3.2 (A), K1.COIL2, Q1.3 (D)
unnamed: D4.1 (K), R6.1
unnamed: D5.1 (K), R8.1
unnamed: D7.5 (CO), D8.2 (CI)
unnamed: D7.6 (DO), D8.1 (DI)
unnamed: D8.5 (CO), D9.2 (CI)
unnamed: D8.6 (DO), D9.1 (DI)
unnamed: D9.5 (CO), D10.2 (CI)
unnamed: D10.5 (CO), D11.2 (CI)
unnamed: D9.6 (DO), D10.1 (DI)
unnamed: D10.6 (DO), D11.1 (DI)
unnamed: D12.5 (CO), D13.2 (CI)
unnamed: D12.6 (DO), D13.1 (DI)
unnamed: D13.5 (CO), D14.2 (CI)
unnamed: D13.6 (DO), D14.1 (DI)
unnamed: D14.5 (CO), D15.2 (CI)
unnamed: D14.6 (DO), D15.1 (DI)
unnamed: D15.5 (CO), D16.2 (CI)
unnamed: D15.6 (DO), D16.1 (DI)
unnamed: J2.4, R1.2
RESET: SW1.2 (B), U3.J1_3 (RST)
RFID_CS: J5.1, U3.J3_5 (GPIO2)
RFID_RST: J5.7, U3.J3_18 (GPIO21)
SCK: J4.4, J5.2, U3.J3_10 (GPIO38)
SCL: J4.13, R3.2, U3.J3_16 (GPIO48)
SDA: J4.14, R5.2, U3.J3_17 (GPIO47)
TFT_CS: J4.9, U3.J1_7 (GPIO7)
TFT_DC: J4.7, U3.J1_17 (GPIO11)
TFT_RESET: J4.8, U3.J1_18 (GPIO12)
TS_CS: J4.12, U3.J3_13 (GPIO35)
USBA_D+: J8.8, K2.7, U2.1 (I/O1)
USBA_D-: J8.7, K2.8, U2.3 (I/O2)
USBC_D+: J8.14, K2.1, U4.1 (I/O1)
USBC_D-: J8.1, K2.14, U4.3 (I/O2)
USB_RELAY: D5.2 (A), Q2.1 (G), R9.2, TP2.4, U3.J1_15 (GPIO9)

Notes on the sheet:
Mem CS
5->3.3V Regulator Added To run APA102 at 3.3V (Logic high = 0.7*VCC)
Tie ground planes together in case of continued issues
AC POWER
ESP32-C1
SD CS
GPIO/PERIPHERALS
*2oz copper only!*
LEDS
Note: Recommended T1A 420-600V Fuse is challenging to find It has been excluded from this schematic
USB
There are knockoff devkit-C modules which have a different footprint size Pinout is identical

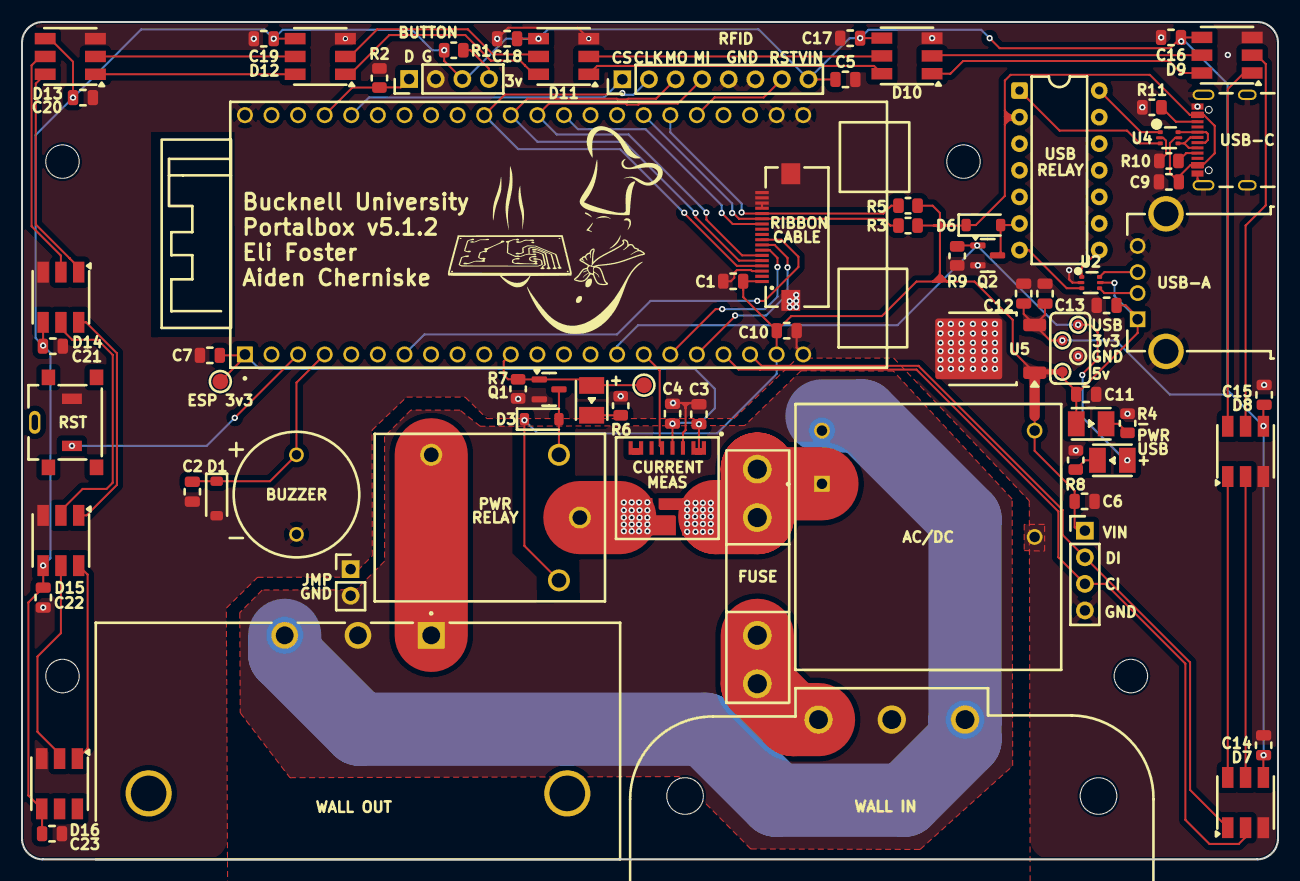
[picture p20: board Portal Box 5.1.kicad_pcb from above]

Board: 2 copper layers, 120.0 x 80.0 mm, 79 parts (0 on the bottom side), 63 nets.

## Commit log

2025-10-25 Add 5.1 Files
    Add 5.1.0 files from version pushed to production for testing.
    [6871XX149022_687118149022.step, 703W-00_53.step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]
2025-10-28 update track clearances, mfg files
    [Portal Box 5.1-B_Cu.gbr, Portal Box 5.1-B_Mask.gbr, Portal Box 5.1-B_Paste.gbr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]
2025-10-28 changed some part numbers, update csv
    [Portal Box 5.1.csv, Portal Box 5.1.kicad_sch]
2025-11-03 update current implementation
2026-02-10 update to 5.1.1
    [Portal Box 5.1.kicad_pcb, Portal Box 5.1.kicad_sch]
2026-02-12 change ac/dc and acm to dc ground, update planes
    [Portal Box 5.1.kicad_pcb, Portal Box 5.1.kicad_sch]
2026-02-26 fix ground plane bulges, schematic and layout change for TVS diodes
    [Portal Box 5.1.kicad_pcb, Portal Box 5.1.kicad_sch]
2026-02-26 move r2 and fix silkscreening, update tvs diode footprint
    [Portal Box 5.1.kicad_pcb]
2026-02-26 update revision number :)
    [Portal Box 5.1.kicad_pcb]
2026-03-03 schematic updates, added ground jumper
    [Portal Box 5.1.kicad_pcb, Portal Box 5.1.kicad_sch]
2026-03-05 update component labels
    [Portal Box 5.1.kicad_pcb, Portal Box 5.1.kicad_sch]
2026-03-16 chore: fix labels, solid pad connections, and version no.
    [Portal Box 5.1.kicad_pcb, Portal Box 5.1.kicad_sch]
2026-03-17 fix drc errors and remove tp4 reference
    [Portal Box 5.1.kicad_pcb, Portal Box 5.1.kicad_sch]
